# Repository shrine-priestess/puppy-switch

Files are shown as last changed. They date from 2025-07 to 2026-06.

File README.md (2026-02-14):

Now available at Just Cuz Robotics!
https://justcuzrobotics.com/products/puppy-power-switch-fail-on-screw-switch?_pos=1&_sid=834575449&_ss=r

# P.U.P.P.Y. Fail-On Power Switch

The P.U.P.P.Y. Switch (the Proven Unit for Perpetual Power, Y’know?) is the first commercially available fail-on switch designed for beetleweight combat robots! It’s battle-tested and built to keep your bot powered on through even the toughest matches. Designed by Kezia Skye, builder and driver of Chainsaw Kitty, this is the same switch that powered Kitty to victory at NHRL’s April 2025 event, where she claimed her Golden Dumpster. Each switch is assembled by hand and tested before shipping to ensure it’s ready for combat.

At 6.5g, it’s not the lightest switch available, but it trades weight for reliability and straightforward operation. Threaded M2 inserts in the case make mounting easy, and the 2.5mm hex drive screw offers easy power cycling. If you’re running a bot that needs to take hits and keep moving, this little pup’s ready to work.

!! Be sure to read the setup guide before setting up your puppy! It includes critical info about correct soldering, tab installation, and usage of the switch.

# What is a Fail-On Switch?

Other beetleweight power switches rely on tightening a screw to make contact and power the robot. But that connection has to stay tight through all the vibration and violent impacts of a match. If it loosens, your bot can shut down mid-fight!

The P.U.P.P.Y. Switch takes the opposite approach. It’s a fail-on switch, meaning the default state is powered on, and the screw only comes into play when powering down. A strong internal spring keeps the switch closed and your bot powered through even the roughest hits. Once your pup is awake, it’s staying that way until you say otherwise!

# Features and Specs

-Weight: 6.5 grams (0.23oz)

-Size: 18mm x 20mm x 10mm (plus 3.75mm copper stick-out)

-Drive: 2.5mm hex, screw is captive and cannot escape the casing

-Mounting: 2x threaded M2 inserts in case, 11mm center-to-center distance

-Wiring: Copper tabs accept up to 16 AWG through-hole, larger gauges can lay flat or be partially through-hole

-Voltage: Tested up to 8s LiHV (34.8v). Added precharge recommended for over 4s.

-For Use In: Any beetleweight robot!

-Switch disassembles easily for service!

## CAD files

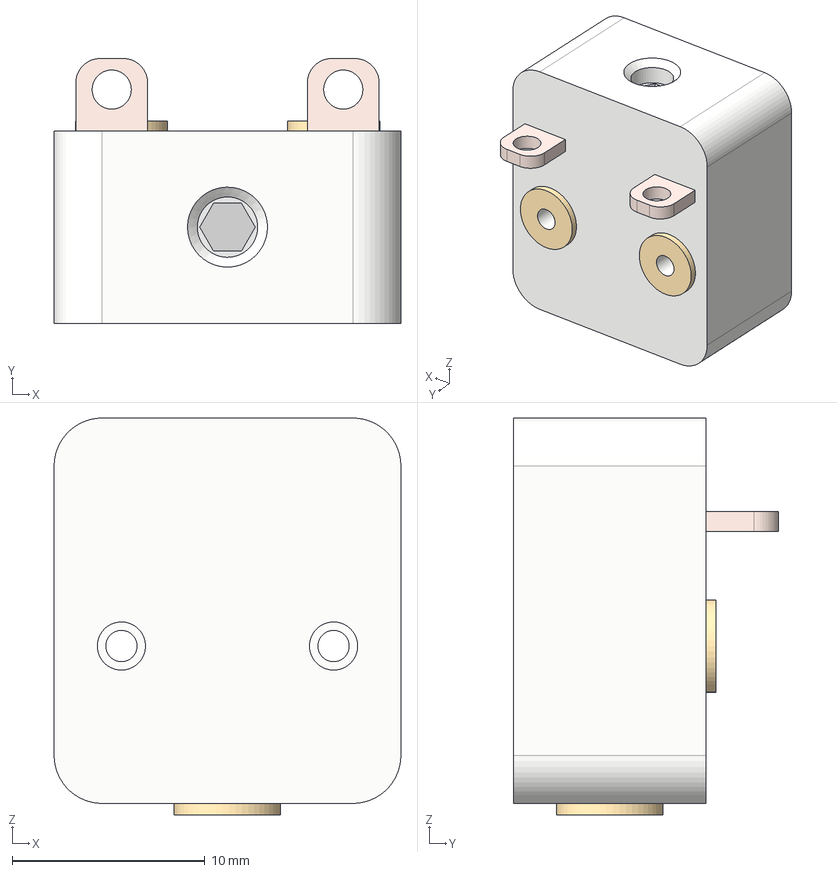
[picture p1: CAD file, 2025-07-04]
PUPPY v3 reference v2.step
18.0 x 13.7 x 20.6 mm

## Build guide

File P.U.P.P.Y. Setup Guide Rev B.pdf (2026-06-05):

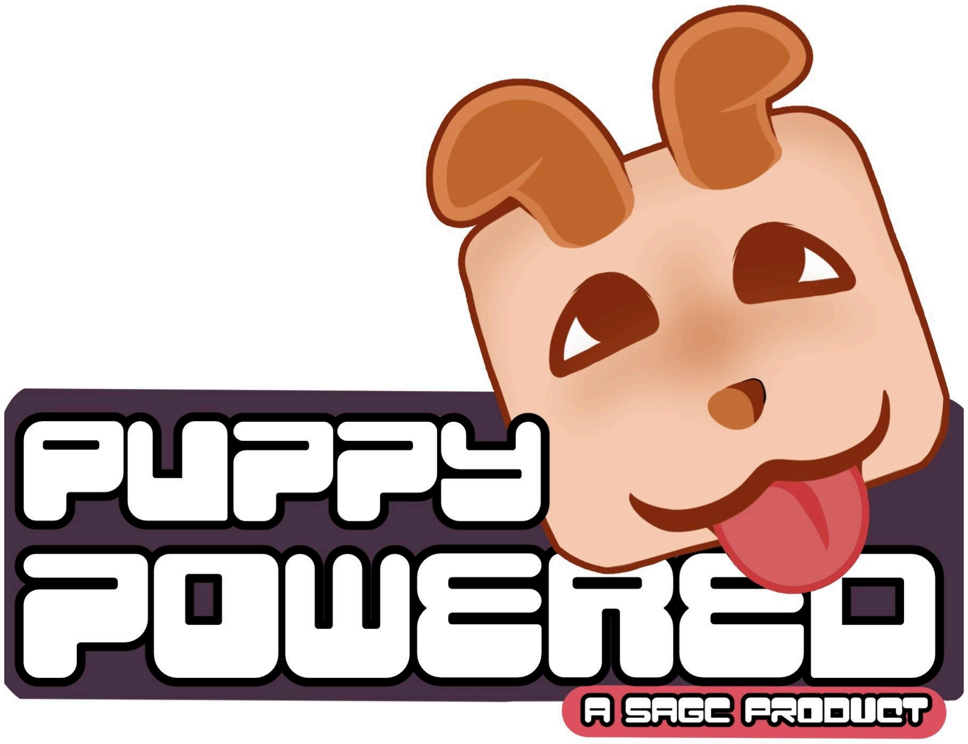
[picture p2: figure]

Thank you for choosing to adopt the P.U.P.P.Y. Switch! This guide will help you get set up and running with your new companion. Setup is simple, but there are a few important things to keep in mind. Please read through carefully before getting started!

# Section 1: Opening your Puppy

Use a small flathead screwdriver or similar prying tool to gently open the case.

Insert at the seam between the “nose” and “eyes” on either side, and your puppy should then pull apart easily.

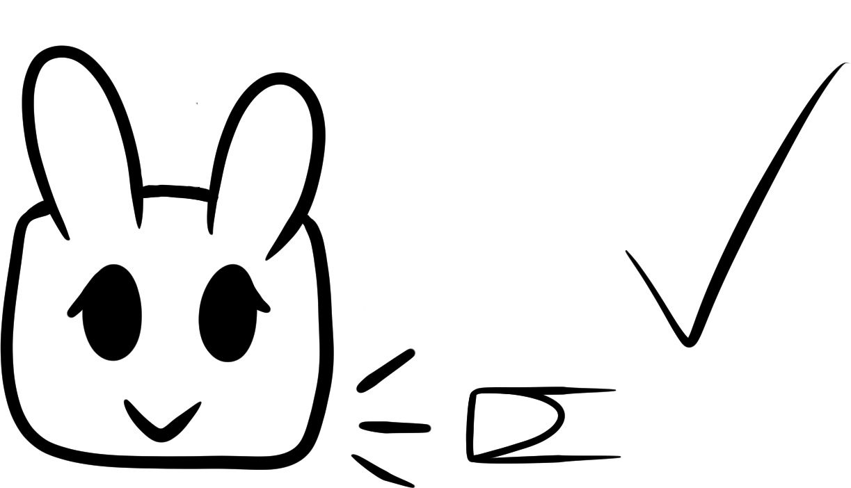
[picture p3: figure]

Twist the copper tabs (inner edge upwards!) then pull forward to remove them from the casing.

# Section 2: Soldering the Copper Tabs

### Please read this entire section BEFORE soldering!

Never solder the tabs while they are installed in the switch.

The heat can and will injure your puppy! Always remove the tabs before soldering.

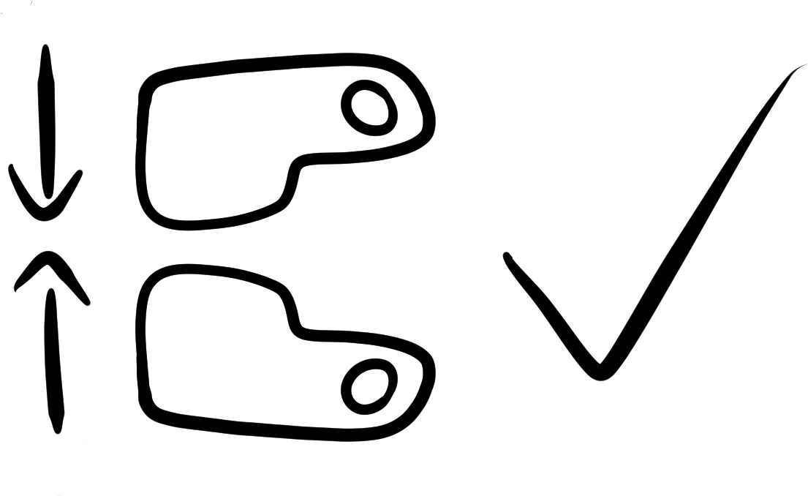
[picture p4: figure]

Pay attention to tab orientation! When installed later, the nubs must face inward toward each other. Keep this in mind when choosing the path your wires will take!

We recommend lightly sanding both copper tabs in the pictured green safe area to help your solder stick, just enough to rough up the surface a bit.

When soldering, be sure to only apply solder within the safe zone. Working too far up may interfere with the case properly closing.

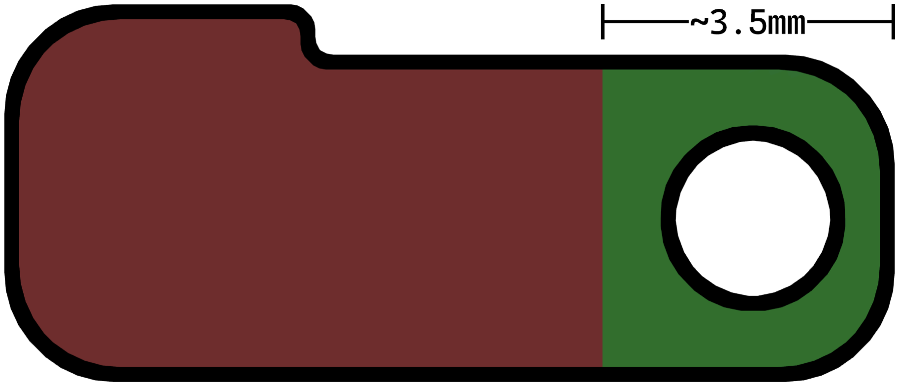
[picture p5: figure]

We recommend soldering the wire through the holes, which support up to 16 AWG. If you're using thicker wire, it can be laid flat on top or partially threaded through the hole.

If you’ve made itthis far without soldering, good job! You are now authorized to do so!

# Section 3: Switch Reassembly

Before inserting the tabs, fully tighten the power screw (clockwise) until snug. This sets the switch to the fully off position, and ensures the internal copper contact won’t interfere with the installation of the tabs!

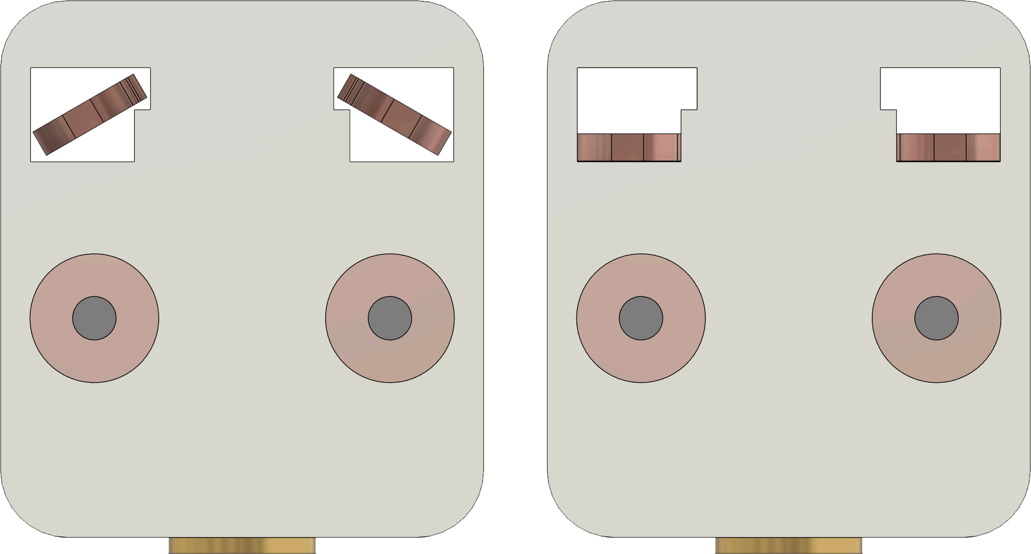
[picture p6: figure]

Make sure the nubbed sides face inward, toward the center of the switch. Insert each tab into its slot at an angle (inward edge up), then twist to lay them flat at the bottom of the opening. Once both tabs are inserted, align the rear of the case, making sure the protrusions fit into the openings above the copper tabs. Press the casing together tightly.

# Section 4: Mounting Your Switch

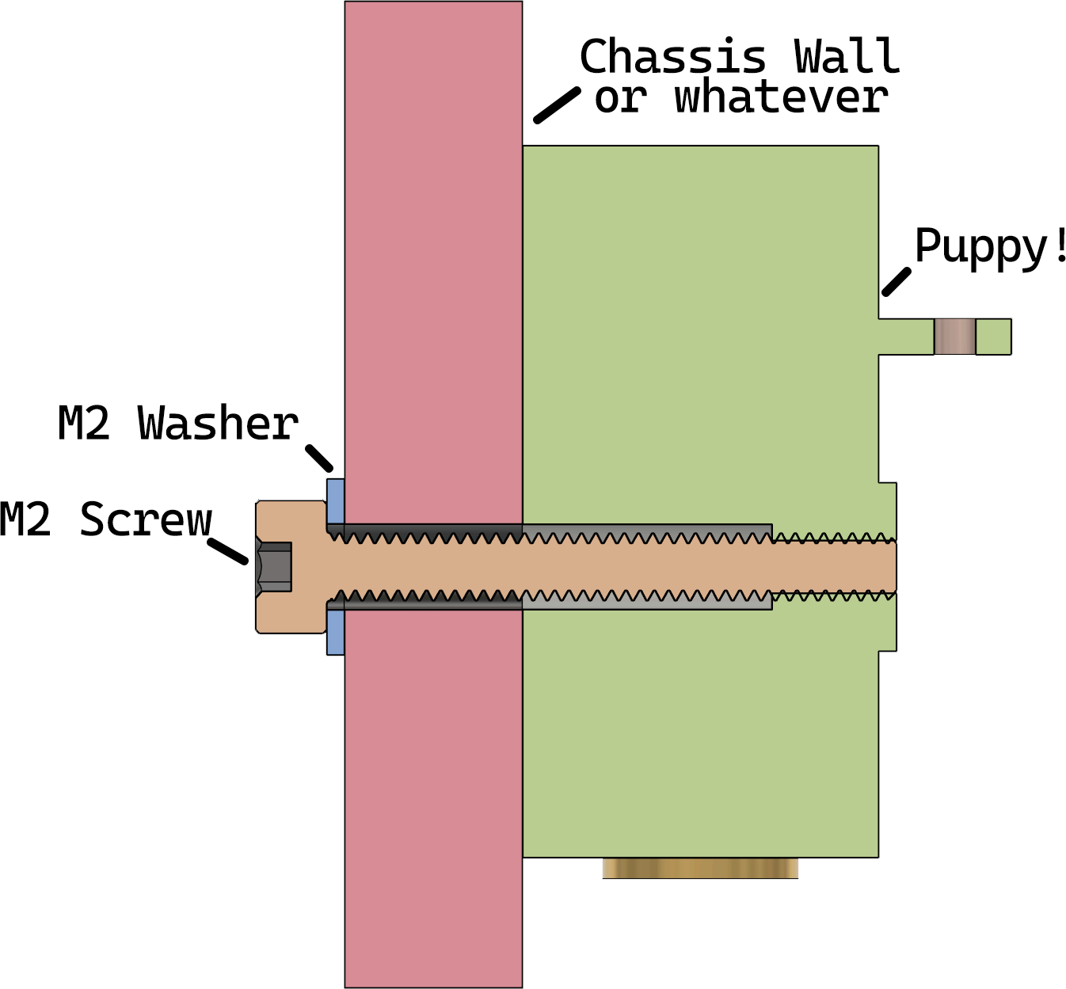
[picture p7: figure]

Insert M2 screws through your chassis wall, mounting plate, or other internal structure, then thread them through your puppy and into its inserts. We recommend adding washers under the screw heads!

Please be aware that both the main power screw and bottom insert are likely live!

# Section 5: Powering On & Off

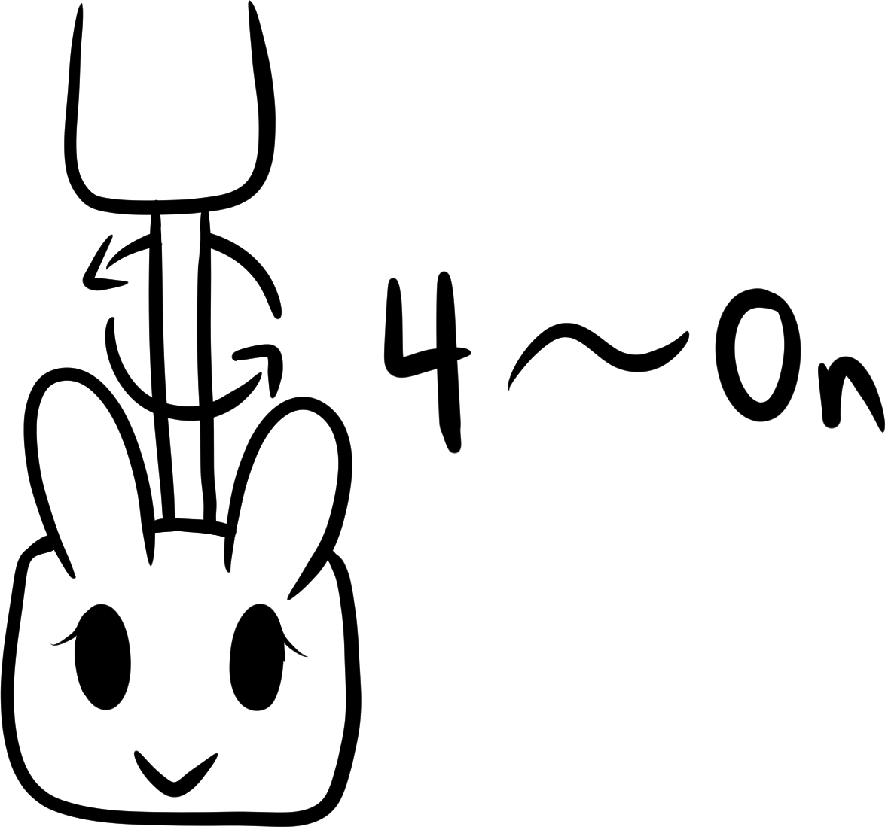
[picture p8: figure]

To activate the switch, turn the power screw approximately four full counterclockwise turns. This is the opposite direction compared to other available switches! Once you feel firm resistance, stop turning! Forcing pastthis point can damage your puppy’s casing!

We recommend any long term storage be done with the switch in the on position. This will prolong the life and strength of your puppy’s internal spring!

To deactivate the switch, turn the power screw approximately four times clockwise until snug.

Do not overtighten! Once the screw is snug, stop turning. Too much force may hurt your puppy!

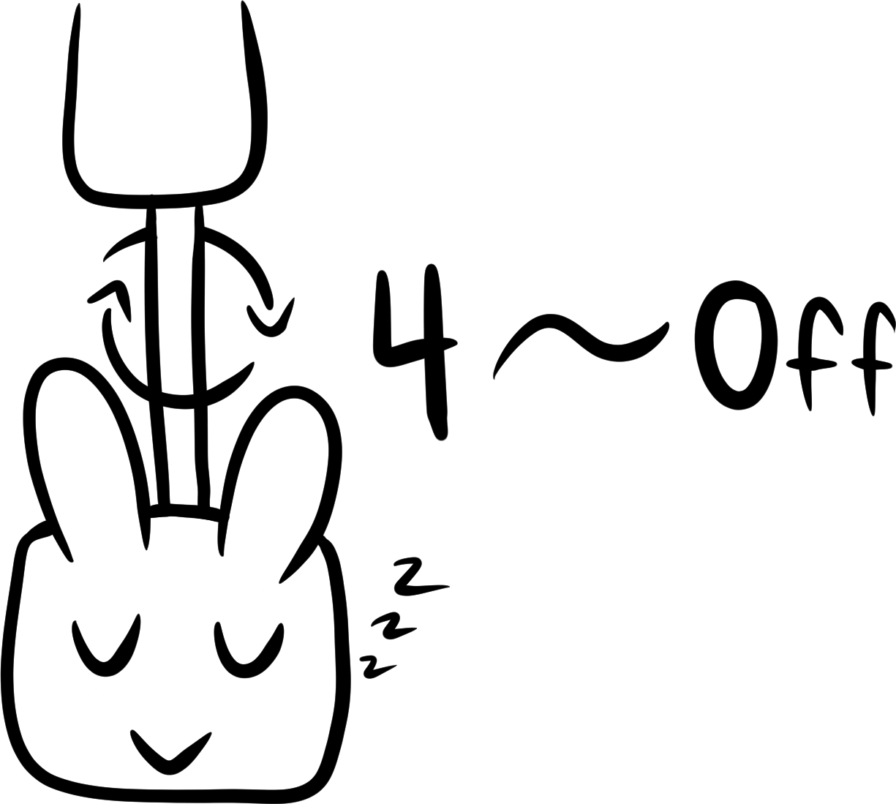
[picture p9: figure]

We hope you enjoy your new switch!
Any questions? Send an email to sleepyanimegirlclub@pm.me, or reach out to Kezia on Discord at .priestess (period at the beginning!)

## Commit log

2025-07-15 Added warning about switch and heat set being live
2026-06-05 New setup guide for latest switch revision
